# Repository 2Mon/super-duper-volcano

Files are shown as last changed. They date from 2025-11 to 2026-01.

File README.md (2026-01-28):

# super-duper-volcano
This is my custom hotend, featuring three 110W supervolcano heaters for quick heat-up times and thermal mass, and three M3 PT1000 thermistors for measuring temperature across the entire 60mm melt zone. The block is made out of nickel-plated copper, and the heatsink is made of aluminum.

I made this because I wanted to make a new hotend for my Voron, without compromising flow rate. This hotend has one of the largest melt zones ever made, and should be able to push at least 80mm/s^3 of ABS out of a .4mm nozzle. This will require a custom toolhead, which I will be designing later. 

Its done!! Huge thanks to everyone who made this project possible, especially @tortlegod, @ruiqimao, @dr.ooof, and lastly PCBWAY, who sponsored the SLM parts for this project!!!! Video coming soon 👀

Screenshot 2026-01-27 at 7 48 35 PM

Screenshot 2025-11-09 at 1 52 34 PM

| Product Name | Link | Price | Quantity | Total |
|---|---|---:|---:|---:|
| SuperVolcano Heaters | [Link](https://www.aliexpress.us/item/3256801135491506.html) | 3.75  | 3 | 11.25 |
| M3 Thermistor | [Link](https://trianglelab.net/products/pt1000-thermistor-cartridge-1) | 12.43 | 3 | 37.29 |
| Smooth Heatbreak | [Link](https://www.aliexpress.us/item/3256808834108668.html) | 1.89  | 1 | 1.89  |
| Hardened Steel Nozzle | [Link](https://www.aliexpress.us/item/3256807972374706.html) | 4.60  | 1 | 4.60  |
| PEEK m2x20 | [Link](https://www.aliexpress.us/item/3256809026195968.html) | 3.22  | 1 | 3.22  |
| CNC Parts | BEING SPONSORED |0 | 1 | 0 |
| M3 Grub Screw | [Link](https://www.aliexpress.us/item/2255800662710347.html) | 1.34  | 1 | 1.34  |

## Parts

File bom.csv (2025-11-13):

Product Name | Link | Price | Quantity | Total
SuperVolcano Heaters | https://www.aliexpress.us/item/3256801135491506.html | 3.75 | 3 | 11.25
M3 Thermistor | https://trianglelab.net/products/pt1000-thermistor-cartridge-1 | 12.43 | 3 | 37.29
Smooth Heatbreak | https://www.aliexpress.us/item/3256808834108668.html | 1.89 | 1 | 1.89
Hardened Steel Nozzle | https://www.aliexpress.us/item/3256807972374706.html | 4.6 | 1 | 4.6
PEEK m2x20 | https://www.aliexpress.us/item/3256809026195968.html | 3.22 | 1 | 3.22
CNC Parts | BEING SPONSORED | 0 | 1 | 0
M3 Grub Screw | https://www.aliexpress.us/item/2255800662710347.html | 1.34 | 1 | 1.34

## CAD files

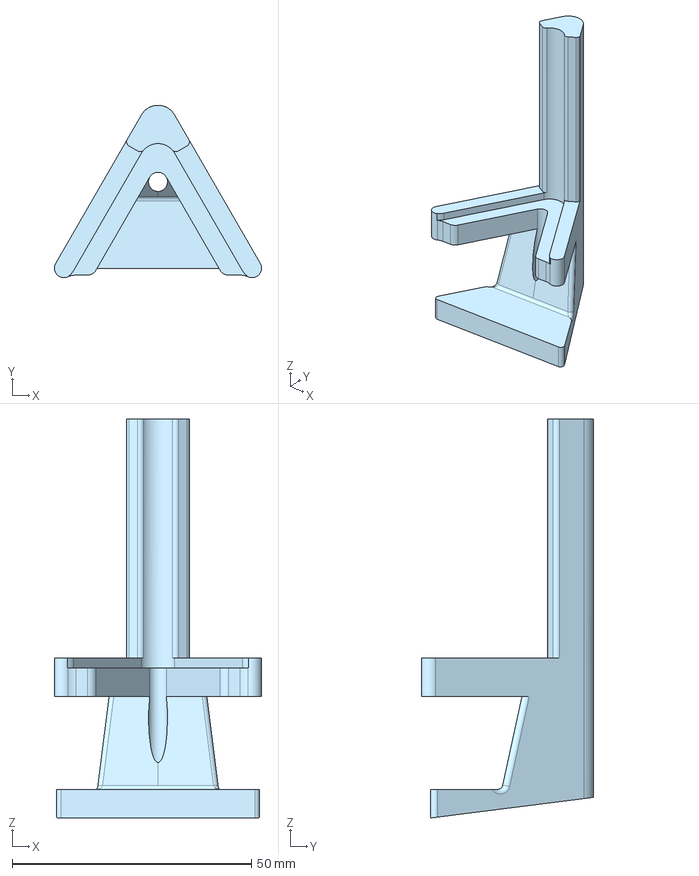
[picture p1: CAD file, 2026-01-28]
CAD/Stand.step
43.3 x 36.0 x 83.4 mm

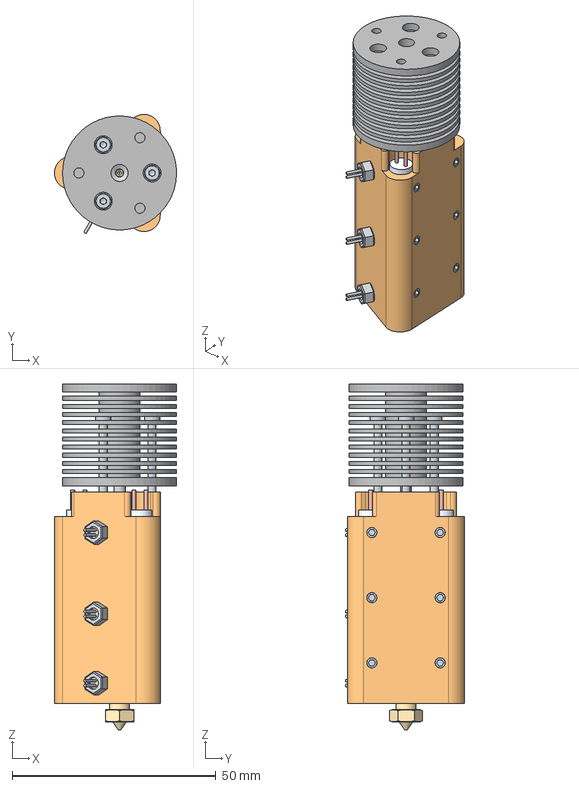
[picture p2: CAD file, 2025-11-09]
CAD/Super Duper Volcano.step
30.0 x 29.3 x 85.0 mm
Hex socket head cap screw M2x0.40 x 20 x 3
Hex socket set screw with cone point M3x0.5 x 3 x 9
E3D v6 HotEnd - Heatbreak (1) (1)
m3 hex thermistor x 3
V6 Nozzle (1) (1)

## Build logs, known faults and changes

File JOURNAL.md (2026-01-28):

## 11/9/2025 12:11 PM - Researched Parts  

_Time spent: 2.0h_  

I started this project by researching parts I want to use for this hotend. 

I first looked at different existing hotends, including Tricorn, which uses multiple different heater cartridges to give more surface area for heat transfer, rather than one larger one. Tricorn uses 3x Volcano heaters, which give much more surface area than a supervolcano heater, while staying compact. 

I decided to take inspiration from Tricorn, but give it even more surface area by using the massive 110W heaters from a supervolcano hotend. 



These heaters are massive, and a single one would be overkill for most hotends, but this is not most hotends. I will be using three of these. 

## 11/9/2025 12:19 PM - Begun Heatblock Design  

_Time spent: 3.0h_  

I started the design of this with the heat block. It has three 6mm holes for three supervolcano heaters, each with three m3 grubscrews to hold them in. It also has an M6 tapped hole in the center where the nozzle will go, along with a 1.8mm hole through the center where the filament will pass through and melt. 



On the other side, it has an M7 tapped hole for the heatbreak mounting, as well as some m2 tapped holes for the bolts that will attach the heatsink to the heater block. Since I like triangles, there are three holes. 

Screenshot 2025-11-09 at 12.17.57 PM

## 11/9/2025 12:36 PM - Heatsink Design  

_Time spent: 2.0h_  

I designed the heatsink in this session. It was fairly simple, just a cylinder with holes for the heatbreak, as well as mounting holes on the top and pass-through holes on the bottom to allow me to tighten the heatsink down to the block. It uses three M2 screws to clamp down on the heatbreak. It has some complex geometry inside, which allows the heatbreak to fit inside, as well as thread in and allow the filament to pass through. It has a hole in the top for the 4mm OD PTFE tube to fit in and push up against the heatbreak. The fins were made using a revolve operation of a sketch I made of each fin. 

Screenshot 2025-11-09 at 12.21.12 PM

## 11/9/2025 12:43 PM - Heatblock Fixes  

_Time spent: 2.5h_  

While doing a test fit in CAD, I realized that the wires for the supervolcano heaters won't be able to get out from the heater block and under the heatsink. I want it to be easy to use IRL, so I added some cutouts for the wires to be able to come out of. 

Screenshot 2025-11-09 at 12.36.36 PM

I also added M3 tapped holes for the three M3 PT1000 thermistors that will measure the temperature across the entire melt zone. This is important as it can vary slightly across the melt zone, so we could average it out and get a more accurate measurement. 

I added the thermistors to the CAD as well.

Screenshot 2025-11-09 at 12.40.36 PM

Here's my full test fit with the block, heaters, thermistors, and the nozzle. 

I colored it orange because I may end up using nickel-plated copper for the block, as it has good thermal conductivity from the copper and good hardness from the nickel plating. This is fairly common with high-quality hotends. 

## 11/9/2025 1:33 PM - Cad Assembly  

_Time spent: 1.0h_  

I added the heatsink and heatbreak to the CAD in this session. You can see the filament path here, as well as way everything goes together. I need to test if the heatsink fins are large enough, as this hotend will be dumping a ton of heat into the heatbreak and subsequently the heatsink. 



## 11/9/2025 1:48 PM - Made BOM  

_Time spent: 0.5h_  

I made the BOM in this session. I used AliExpress and Trianglelabs for most of the parts, but the CNC parts will be from JLCCNC, and the heaters were from Fabreeko. The total price is around 200 dollars. 

Screenshot 2025-11-09 at 1.48.42 PM

## 1/27/2026 7:31 PM - Received the Parts!  

_Time spent: 0.1h_  

I finally got all the parts in!! The SLM parts are a little warped, but it should be fine because none of the dimensions are super precise anyway. 

Screenshot 2026-01-27 at 7.28.04 PM

All of the aliexpress parts also came in, they look great! the heaters are so much bigger than I imagined lol. 

Screenshot 2026-01-27 at 7.29.11 PM

I accidentally ordered the wrong size heatbreak, which means that I needed to buy a new one as well as drill out the heatsink to the right size. It has a nice snug fit!!

Screenshot 2026-01-27 at 7.30.21 PM

This is what I ordered origionally ^^ 

Screenshot 2026-01-27 at 7.30.45 PM

And this is what I wanted. It wasnt too bad to fix but I needed to buy a drill bit and a new tap. 

## 1/27/2026 7:37 PM - Partial Assembly  

_Time spent: 0.1h_  

Here it is after being tumbled and partially assembled. Its really cool that your able to see the difference in color between the steel heat block and the aluminum heatsink! The nozzle and heatbreak went in well after tapping the m6 holes. 

Screenshot 2026-01-27 at 7.32.57 PM

The top looks really cool! the m3 taps for mounting and the bolt heads, along with the filament path through the middle make it really interesting to look at. im really happy with this!! 

Screenshot 2026-01-27 at 7.35.23 PM

Here you can see how the screws go from the heatsink into the heater block. Hopefully they dont conduct too much heat which could lead to heat creep. 

Screenshot 2026-01-27 at 7.34.35 PM

And heres a view from the bottom, where you can see the nozzle and the holes for the heaters. 

Screenshot 2026-01-27 at 7.36.35 PM

Overall im really happy with the assembly so far!  

## 1/27/2026 7:41 PM - Designed Stand  

_Time spent: 2.0h_  

While waiting for some parts, I decided to make a nice stand for it! Since this is a gift for my friend, i thought a way to display it would be nice since its not very practical to use. This didnt take me very long, maybe 2 hours, but I went through a couple iterations before landing on the current design.
 
Here you can see the first design (really ugly) 

Screenshot 2026-01-27 at 7.39.05 PM

And here you can see the final desigh (pretty clean imo!!)

Screenshot 2026-01-27 at 7.37.50 PM

I printed it out and it looks pretty nice!  

## 1/27/2026 7:45 PM - Its Finished!  

_Time spent: 0.1h_  

Its finished!! My friend did some super nice cable braiding for the super long heater cables and I think it looks super good!

Screenshot 2026-01-27 at 7.41.32 PM

He also wrapped and shipped it out to my friend!! I had so much fun designing and building this secret santa gift...  

Screenshot 2026-01-27 at 7.43.13 PM

## 1/27/2026 7:47 PM - Gift Delivery!!!  

_Time spent: 0.1h_  

My friend loved it!!!
This was his first reaction:

[Screenshot 2026-01-27 at 7.45.48 PM](/user-attachments/blobs/proxy/eyJfcmFpbHMiOnsiZGF0YSI6OTM0OTQsInB1ciI6ImJsb2JfaWQifX0=--1c20fd78329f7ead602cd49570a757523bfca24a/Screenshot%202026-01-27%20at%207.45.48%E2%80%AFPM.png)

And heres a pic of it on his desk. TYSM blueprint and Hack Club for giving me a grant for this project!! 

Screenshot 2026-01-27 at 7.45.21 PM
